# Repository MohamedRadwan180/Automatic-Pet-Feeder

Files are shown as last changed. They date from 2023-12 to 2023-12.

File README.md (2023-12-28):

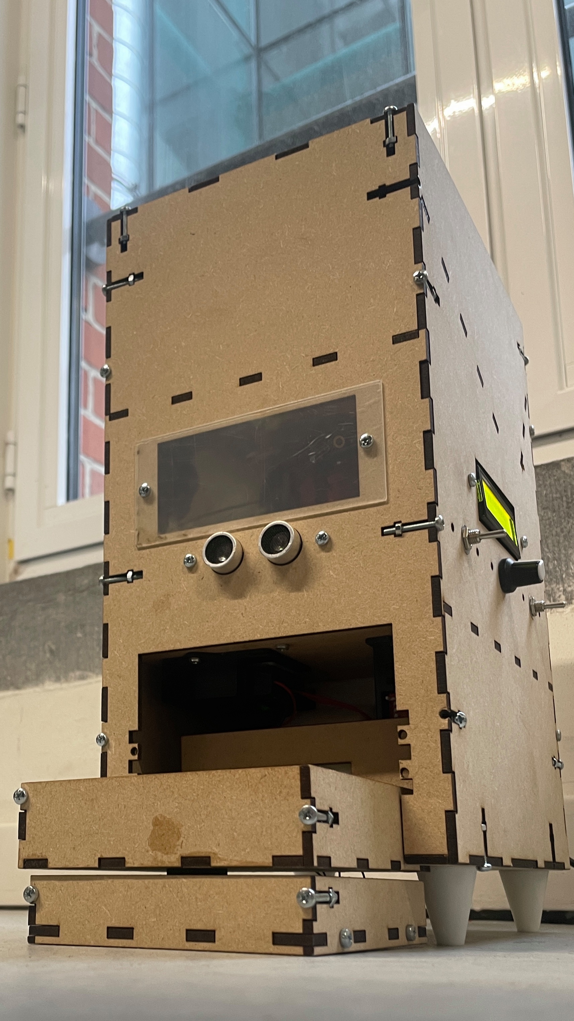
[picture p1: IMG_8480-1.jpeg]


This report describes the design and construction of the prototype of a “Cat Automatic Feeder and Entertainer” carried out in Design Methodology and Mechatronics 1 subjects at VUB as part of the Bruface master of mechantronics at VUB and ULB universities. The idea is simple: building a device that can take care of a cat during a long weekend, taking care of their nutrition and mental health. It will be able to feed the pet the appropriate amount of food at feeding times. In addition, whenever necessary, it will provide an entertaining game to clear the cat's mind. The origin of this idea stems from the lack of a complete product in the market and the need for cat owners to be unconcerned about their cats for a few days. 

The design will consider every possible constraint to achieve all the objectives, such as safety and correct feeding. The building has been developed by laser-cutting for simple and flat parts pieces and 3D printing for more complex ones. The whole design has been carefully designed to consider the space requirements of all components. The materials have been chosen to achieve ecological and functional requirements. 

The electronics and programming subsystems have been implemented in an Arduino Uno, using different modules to take every signal and control the actuators when necessary. Every sensor and motor has been deeply researched to understand the required power supply and code to define the inputs and outputs. 

Every subsystem has been tested before being implemented into the general system. In this way, unique errors can be detected and solved.

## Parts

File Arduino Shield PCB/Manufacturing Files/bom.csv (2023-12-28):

Designator | Footprint | Quantity | Value | LCSC Part #
A1 | Arduino_UNO_R3 | 1 | Arduino_UNO_R3
J1 | JST_EH_B4B-EH-A_1x04_P2.50mm_Vertical | 1 | Conn_01x04_Socket
J10, J7, J8 | TerminalBlock_bornier-2_P5.08mm | 3 | Conn_01x02_Pin
J11 | PinHeader_1x09_P2.54mm_Vertical | 1 | Conn_01x09_Pin
J12, J3, J4, J5 | PinHeader_1x03_P2.54mm_Vertical | 4 | Conn_01x03_Pin
J2, J6 | PinHeader_1x04_P2.54mm_Vertical | 2 | Conn_01x04_Pin
J9 | PinHeader_1x04_P2.54mm_Vertical | 1 | Conn_01x04_Socket

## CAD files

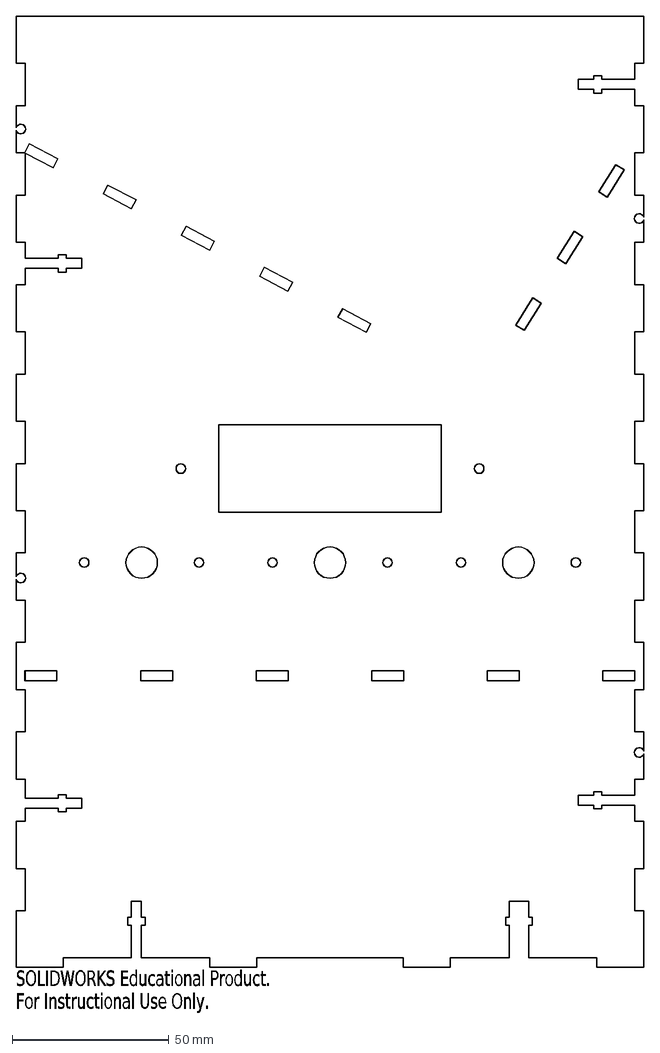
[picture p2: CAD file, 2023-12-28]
Mechanical Design CAD - Solidworks/CAT Feeder Box Franki/Pieza1-Brida base399.DXF
SOLIDWORKS Educational Product.
For Instructional Use Only.

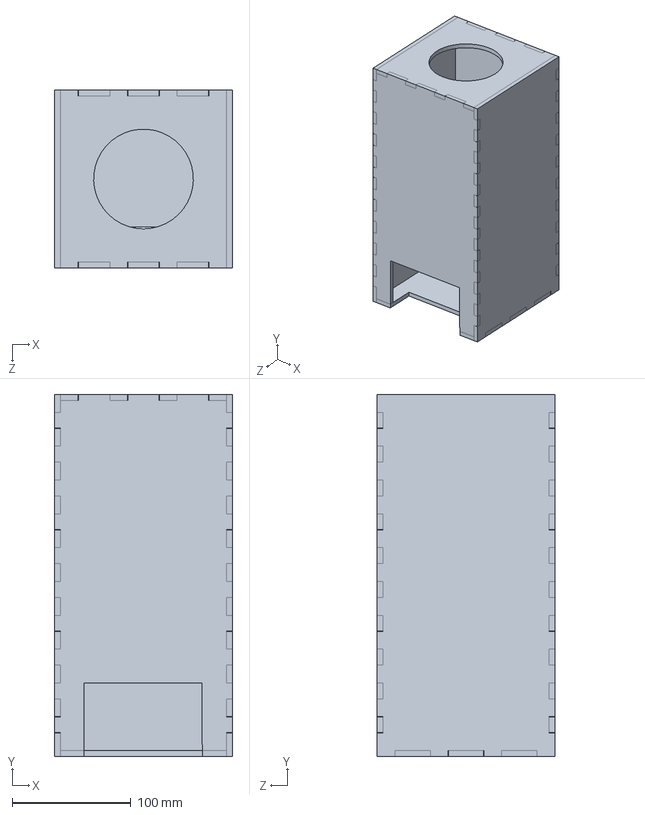
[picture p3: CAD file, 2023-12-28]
Mechanical Design CAD - Solidworks/cat feeder box-20231121T074059Z-001/cat feeder box/Pieza1.SLDPRT
150.0 x 305.0 x 150.0 mm

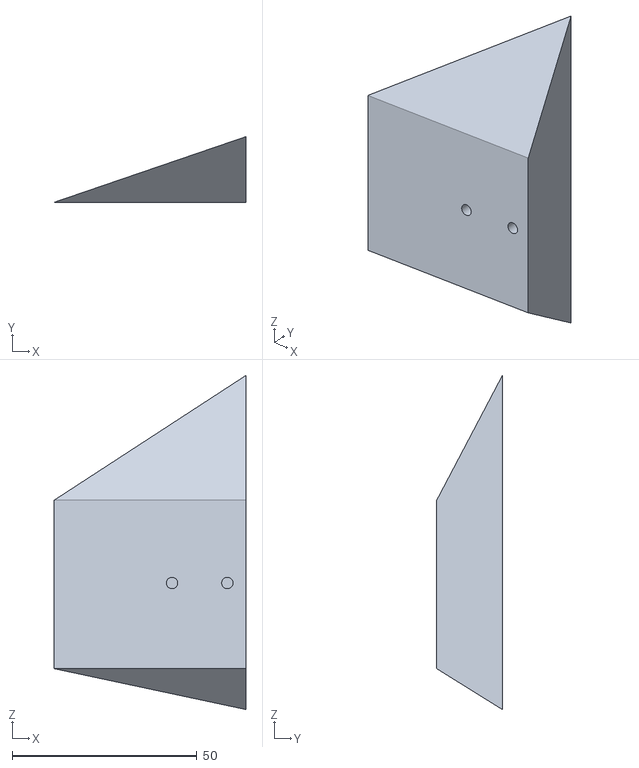
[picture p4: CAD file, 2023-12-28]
Mechanical Design CAD - Solidworks/Laser Pointing System/3d printing/Pieza1-Boss-Extrude4.STL
51.9 x 17.8 x 90.5

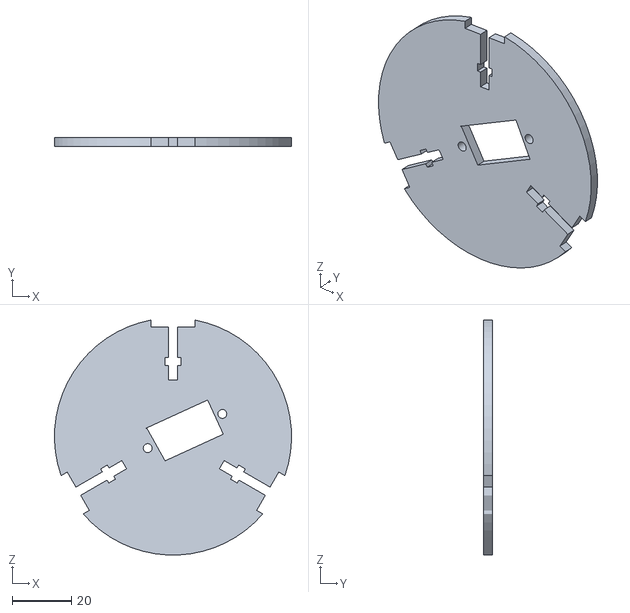
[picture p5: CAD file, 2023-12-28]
Mechanical Design CAD - Solidworks/Laser Pointing System/Motor Base Ring-Cut-Extrude5.STL
80.0 x 3.00 x 79.2

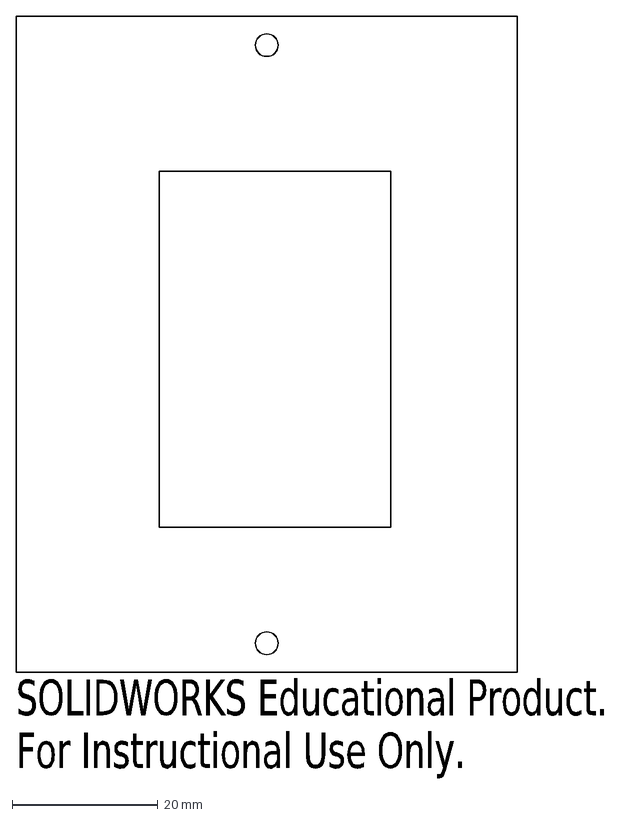
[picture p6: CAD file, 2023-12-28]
Mechanical Design CAD - Solidworks/Plate-Franki/laser cutter/case/Pieza1-Boss-Extrude8.DXF
SOLIDWORKS Educational Product.
For Instructional Use Only.

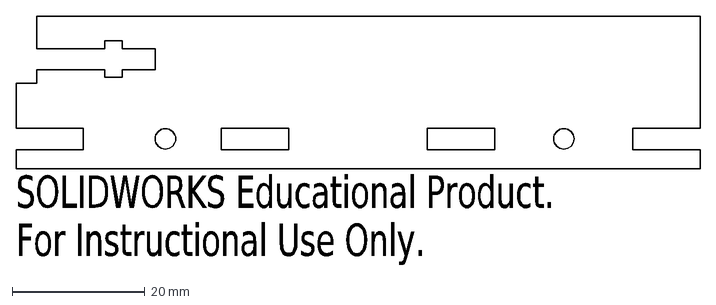
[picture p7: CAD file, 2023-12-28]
Mechanical Design CAD - Solidworks/Plate-Franki/laser cutter/plate/Pieza2-plate-Brida base7.DXF
SOLIDWORKS Educational Product.
For Instructional Use Only.

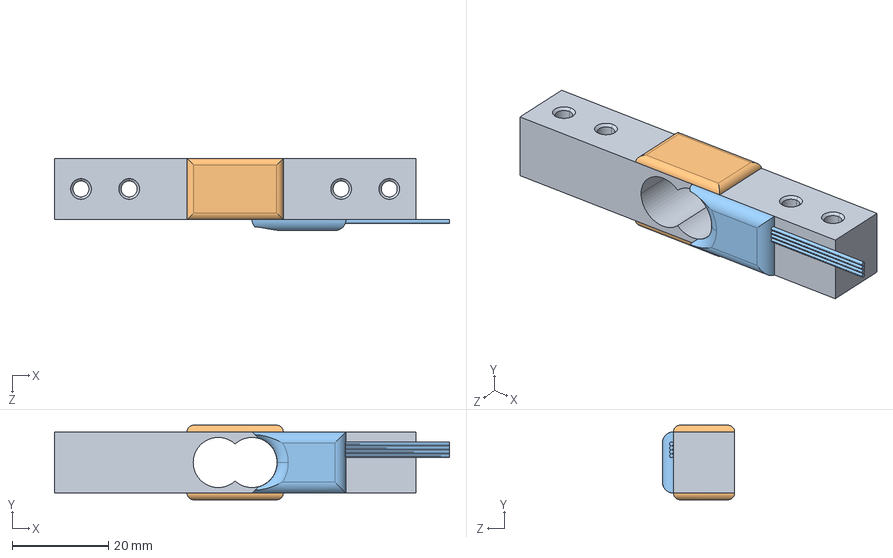
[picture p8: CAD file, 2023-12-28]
Mechanical Design CAD - Solidworks/Plate-Franki/Plate/weight sensor FHDA.STEP
82.0 x 15.5 x 15.0 mm

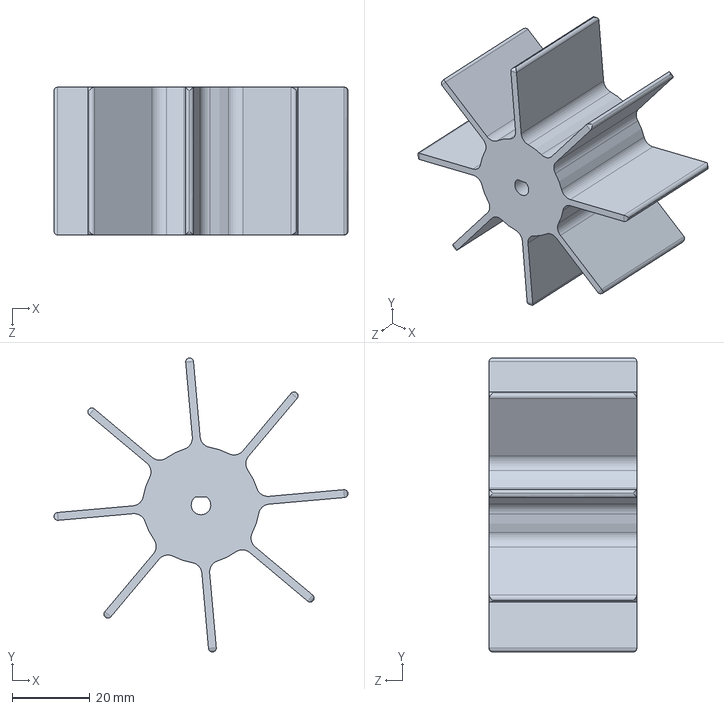
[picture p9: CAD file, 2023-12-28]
Mechanical Design CAD - Solidworks/wheel rotation/Food Dispenser-Boss-Extrude1.SLDPRT
75.6 x 75.6 x 38.0 mm

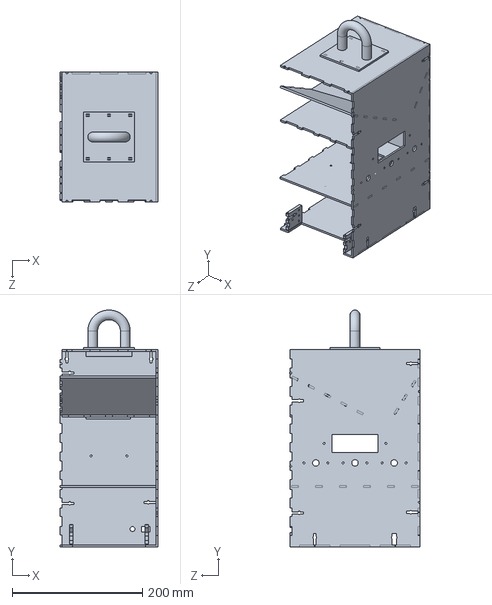
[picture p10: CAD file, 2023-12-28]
Mechanical Design CAD - Solidworks/CAT Feeder Box Franki/Pieza1.SLDPRT
150.0 x 363.5 x 200.0 mm

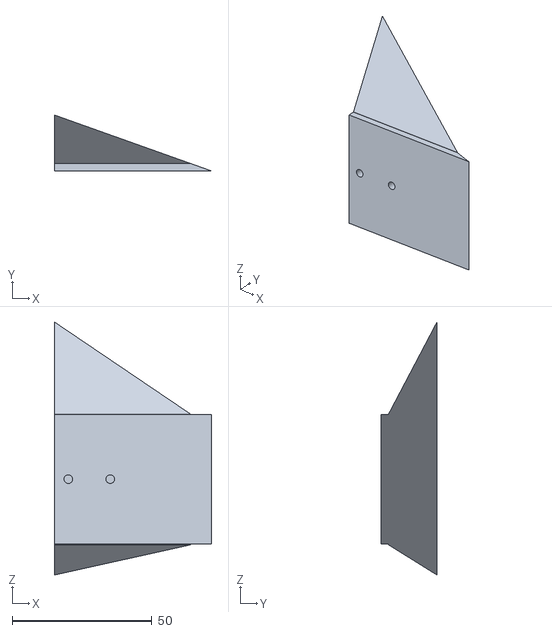
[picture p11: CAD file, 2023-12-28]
Mechanical Design CAD - Solidworks/Laser Pointing System/3d printing/Pieza1-Combine1.STL
56.2 x 20.0 x 90.5

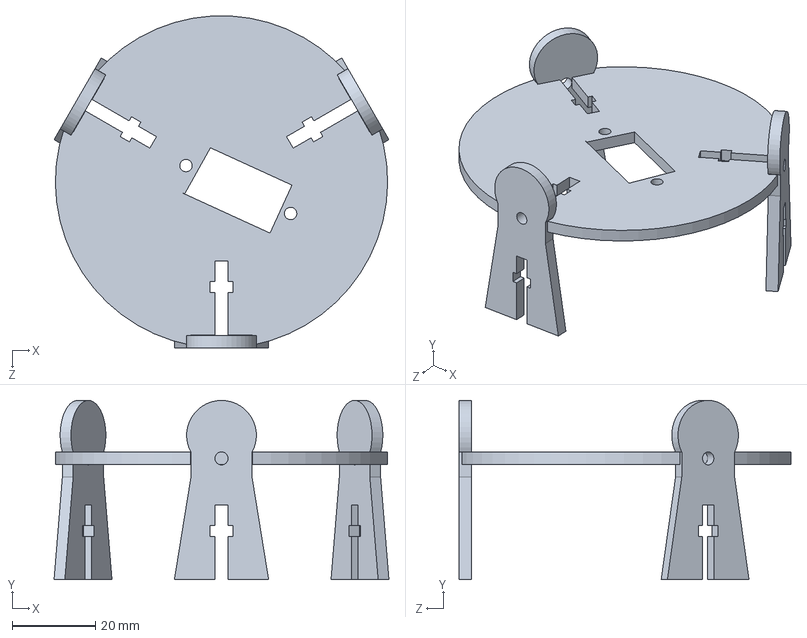
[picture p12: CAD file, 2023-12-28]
Mechanical Design CAD - Solidworks/Laser Pointing System/Motor Base Ring.SLDPRT
80.6 x 43.1 x 79.9 mm

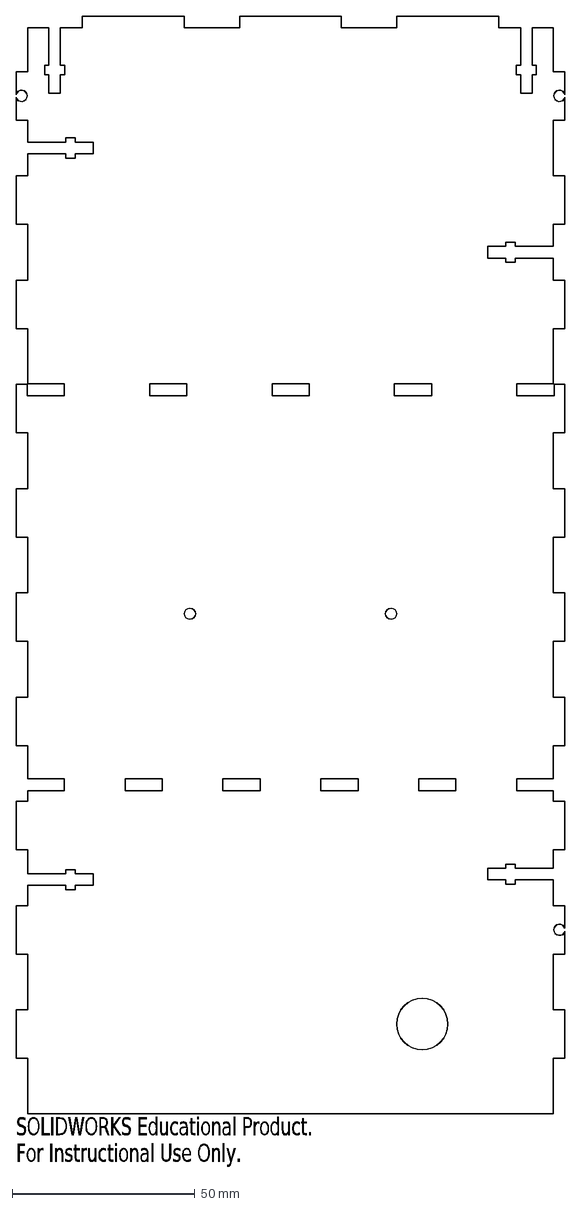
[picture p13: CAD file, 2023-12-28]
Mechanical Design CAD - Solidworks/Plate-Franki/laser cutter/case/Pieza1-Brida base4.DXF
SOLIDWORKS Educational Product.
For Instructional Use Only.

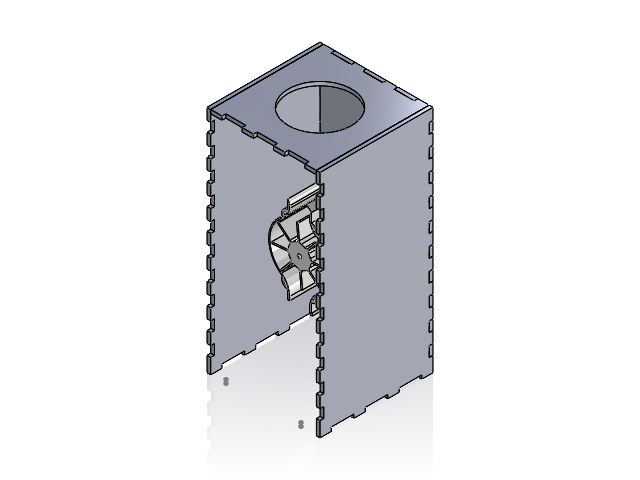
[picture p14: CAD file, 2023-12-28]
Mechanical Design CAD - Solidworks/Mechatronics_Full_Assembly.SLDASM
Pieza1
Food Dispenser
NEMA 17HS13-0404S1
Part1^Mechatronics_Full_Assembly

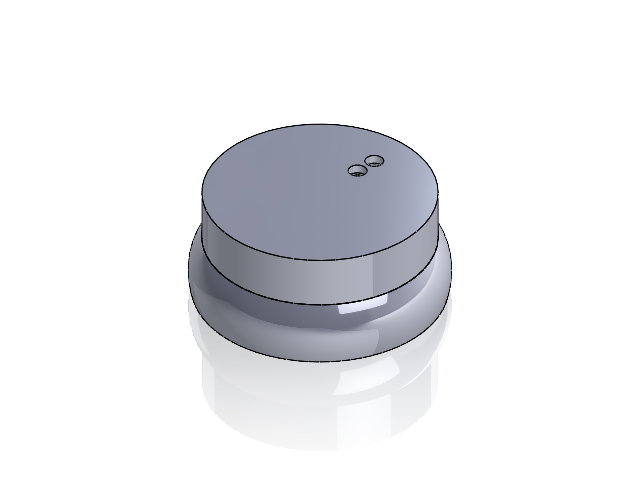
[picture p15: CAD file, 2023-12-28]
Mechanical Design CAD - Solidworks/Bowl_System.SLDASM
load cell sensor
Part1^Bowl_System
Part2^Bowl_System
Bowl
Part4^Bowl_System

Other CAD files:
Mechanical Design CAD - Solidworks/Laser Pointing System/Laser_Pointing.SLDASM
Mechanical Design CAD - Solidworks/Plate-Franki/Plate/Food-Plate.SLDASM
Mechanical Design CAD - Solidworks/Feeding_System.SLDASM
Mechanical Design CAD - Solidworks/cat feeder box-20231121T074059Z-001/cat feeder box/Dibujo Lcutter.DXF
Mechanical Design CAD - Solidworks/Bolt_Nut.SLDASM
Mechanical Design CAD - Solidworks/Bowl.SLDPRT
Mechanical Design CAD - Solidworks/CAT Feeder Box Franki/Pieza1-Brida base3-corrected.DXF
Mechanical Design CAD - Solidworks/CAT Feeder Box Franki/window.DXF
Mechanical Design CAD - Solidworks/CAT Feeder Box Franki/window.SLDPRT
Mechanical Design CAD - Solidworks/Dispenser_Holder.SLDPRT
Mechanical Design CAD - Solidworks/Food Dispenser.SLDPRT
Mechanical Design CAD - Solidworks/Leveling_Pins.SLDPRT
Mechanical Design CAD - Solidworks/Plate-Franki/Plate/111.DXF
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

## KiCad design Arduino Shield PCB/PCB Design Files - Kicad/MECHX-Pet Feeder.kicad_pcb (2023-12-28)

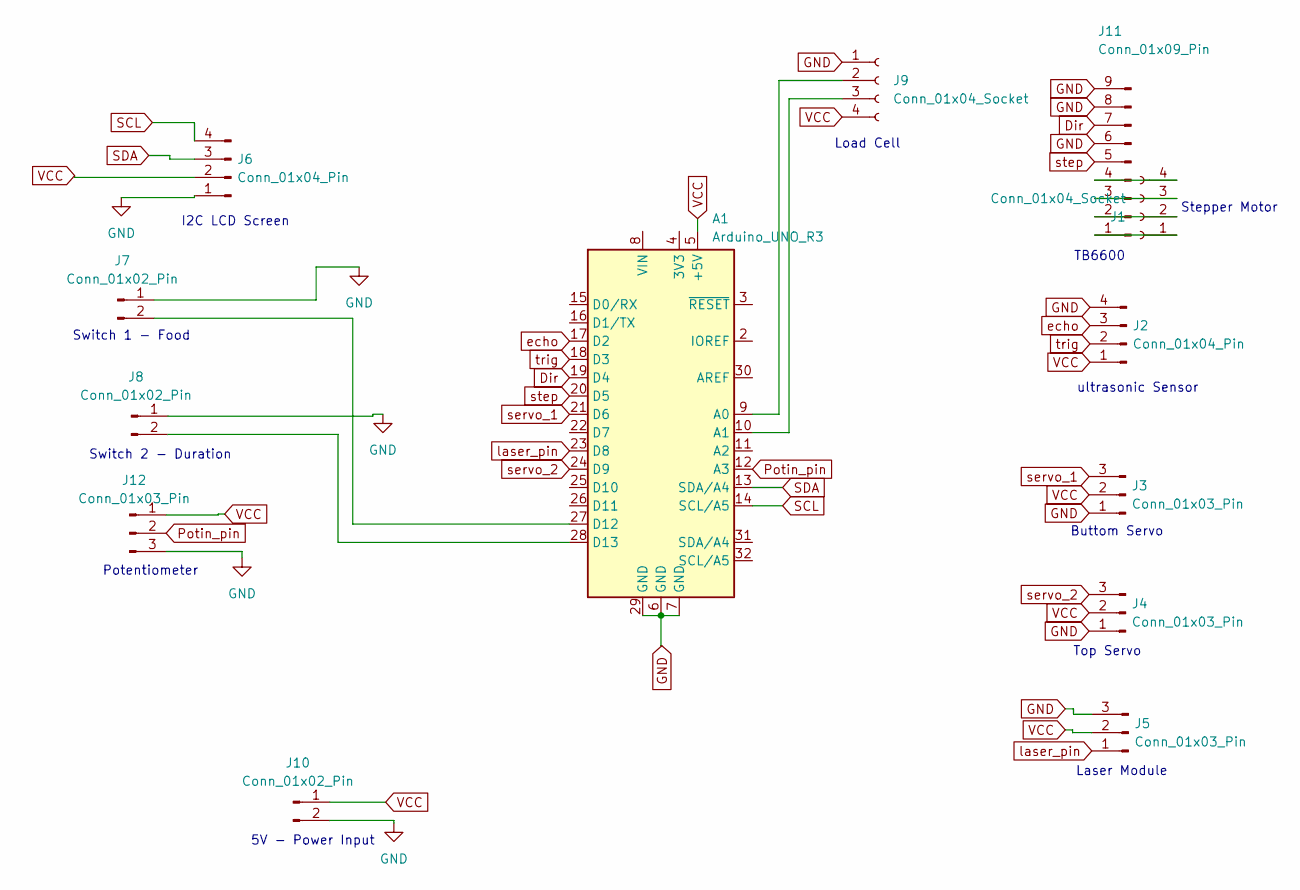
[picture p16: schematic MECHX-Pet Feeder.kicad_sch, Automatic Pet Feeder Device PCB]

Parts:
A1: Arduino_UNO_R3
J1: Conn_01x04_Socket; JST_EH_B4B-EH-A_1x04_P2.50mm_Vertical
J2, J6: Conn_01x04_Pin; PinHeader_1x04_P2.54mm_Vertical
J3, J4, J5, J12: Conn_01x03_Pin; PinHeader_1x03_P2.54mm_Vertical
J7, J8, J10: Conn_01x02_Pin; TerminalBlock_bornier-2_P5.08mm
J9: Conn_01x04_Socket; PinHeader_1x04_P2.54mm_Vertical
J11: Conn_01x09_Pin; PinHeader_1x09_P2.54mm_Vertical

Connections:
Dir: A1.19 (D4), J11.7
GND: A1.6 (GND), A1.7 (GND), A1.29 (GND), J2.4, J3.1, J4.1, J5.3, J6.1, J7.1, J8.1, J9.1, J10.2, J11.6, J11.8, J11.9, J12.3
unnamed: A1.9 (A0), J9.2
unnamed: A1.10 (A1), J9.3
unnamed: A1.27 (D12), J7.2
unnamed: A1.28 (D13), J8.2
unnamed: J1.1, J11.1
unnamed: J1.2, J11.2
unnamed: J1.3, J11.3
unnamed: J1.4, J11.4
Potin_pin: A1.12 (A3), J12.2
SCL: A1.14 (SCL/A5), J6.4
SDA: A1.13 (SDA/A4), J6.3
VCC: A1.5 (+5V), J2.1, J3.2, J4.2, J5.2, J6.2, J9.4, J10.1, J12.1
echo: A1.17 (D2), J2.3
laser_pin: A1.23 (D8), J5.1
servo_1: A1.21 (D6), J3.3
servo_2: A1.24 (D9), J4.3
step: A1.20 (D5), J11.5
trig: A1.18 (D3), J2.2

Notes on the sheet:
Switch 2 - Duration
5V - Power Input
Laser Module
Buttom Servo
Top Servo
Load Cell
I2C LCD Screen
ultrasonic Sensor
TB6600
Potentiometer
Stepper Motor
Switch 1 - Food

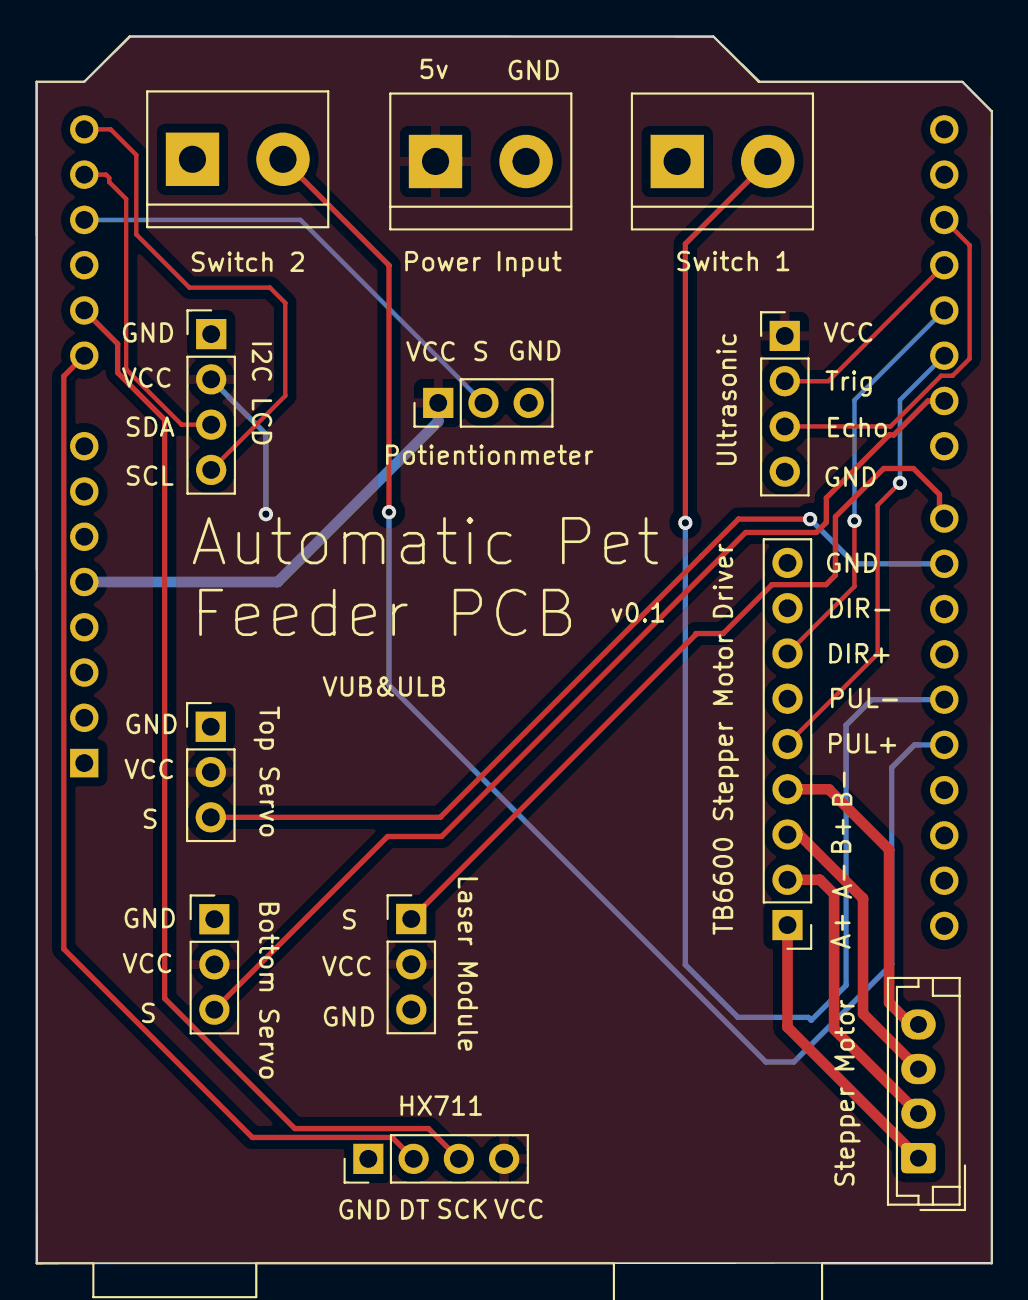
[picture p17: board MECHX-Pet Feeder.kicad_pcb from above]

Board: 2 copper layers, 53.6 x 68.9 mm, 13 parts (0 on the bottom side), 20 nets.

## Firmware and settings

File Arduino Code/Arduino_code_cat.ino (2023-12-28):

#include "HX711.h"
#include <Wire.h>
#include <LiquidCrystal_I2C.h>
#include <Servo.h>

#define dirPin 4
#define stepPin 5
#define FstepsPerRevolution 99
#define BstepsPerRevolution 50
// HX711 circuit wiring
const int Load_cell_DOUT_pin = A0;
const int LOad_cell_SCK_pin = A1;
bool first_time = true;
float c;
HX711 scale;
float weight_2;

//interface
LiquidCrystal_I2C lcd(0x27, 16, 2);  // Déclare l'écran LCD I2C avec son adresse et dimensions (16 colonnes et 2 lignes)
int switch_1_food_amount = 12;
int switch_2_duration = 13;
int potint = A3;
int potint_val = 0;
int portion_size = 10;
int food_duration = 10000; 
int food_status;
int timing_status;

long current_time;
long start_program;

//Entertainment
Servo servoX;
Servo servoY;
/////// Pin laser 
const int laserPin = 8; // Laser control pin
int posX = 90; // Initial position on X axis
int posY = 90; // Initial position on Y axis

// Total number of points to draw
int totalPoints = 10;
int laserDelay = 200; // Laser flash delay (in milliseconds)
int moveDelay = 500; // Delay between moves (in milliseconds)
int enter_start_time;
int enter_current_time;

////// Code for the ultrasonic sensor
float distance;
int currentState;
bool previousState = false; // the cat is not detected. Initial status
const int echoPin_ultrasonic = 2;
const int trigPin_ultrasonic = 3;
int entertainment_limit = 400;
//////

void initiate_settings()
{
  food_status = digitalRead(switch_1_food_amount);
  Serial.println(food_status);

  if(food_status == 1)
  {
    lcd.setCursor(0, 0);
    lcd.print("Portion Size?");
       lcd.setCursor(15, 1);
      lcd.print("g");
  while(food_status == 1)
  {
    
    potint_val = analogRead(potint);
    portion_size = map(potint_val, 0, 1023, 0, 200);
    food_status = digitalRead(switch_1_food_amount);
      lcd.setCursor(0, 1);
      lcd.print(portion_size);
   
      delay(100);
  }
  }
  else
  {
    lcd.clear();
  }

    timing_status = digitalRead(switch_2_duration);
  Serial.println(timing_status);

  if(timing_status == 1)
  {
    lcd.setCursor(0, 0);
    lcd.print("Feeding Duration?");
       lcd.setCursor(13, 1);
      lcd.print("sec");
  while(timing_status == 1)
  {
    
    potint_val = analogRead(potint);
    food_duration = map(potint_val, 0, 1023, 0, 30000);
    timing_status = digitalRead(switch_2_duration);
      lcd.setCursor(0, 1);
      lcd.print(food_duration/1000);
      delay(100);
  }
  }
  else
  {
    lcd.clear();
  }
}

void Dispense(){

    // Set the spinning direction counterclockwise:
  digitalWrite(dirPin, LOW);

  // Spin the stepper motor 1 revolution slowly:
  for (int i=0; i < BstepsPerRevolution; i++) {
    // These four lines result in 1 step:
    digitalWrite(stepPin, HIGH);
    delayMicroseconds(800);
    digitalWrite(stepPin, LOW);
    delayMicroseconds(800);
  }

  delay(100);
     // Set the spinning direction clockwise:
  digitalWrite(dirPin, HIGH);

  // Spin the stepper motor 1 revolution slowly:
  for (int i=0; i < FstepsPerRevolution; i++) {
    // These four lines result in 1 step:
    digitalWrite(stepPin, HIGH);
    delayMicroseconds(600);
    digitalWrite(stepPin, LOW);
    delayMicroseconds(600);
  }

  delay(1000);
}

void activ_laser() {

  for (int i = 0; i < totalPoints; ++i) {
    // Generate random coordinates over a 0.25 m² area (0.5 m x 0.5 m)
    int targetX = random(50, 200); // Range 50 to 200 (0.05 to 0.20 m)
    int targetY = random(50, 200); // Range 50 to 200 (0.05 to 0.20 m)

    // Convertir les coordonnées en positions pour les servomoteurs
    int servoPosX = map(targetX, 50, 200, 50, 120); // Convert range to degrees for X (servo)
    int servoPosY = map(targetY, 100, 200, 140, 150); // Convert range to degrees for Y (servo)

    // Move servos to target coordinates
    servoX.write(servoPosX);
    servoY.write(servoPosY);

    // Activate laser (flashing)
    digitalWrite(laserPin, HIGH);
    delay(laserDelay); // Flash delay

    // Deactivate laser
    digitalWrite(laserPin, LOW);

    // Wait before moving on to the next item
    delay(moveDelay);
  }

}

float fun_distance() {
  // Clear the Trigger pin
  digitalWrite(trigPin_ultrasonic, LOW);
  delayMicroseconds(2);
  // Set the Trigger pin high for 10 microseconds
  digitalWrite(trigPin_ultrasonic, HIGH);
  delayMicroseconds(10);
  digitalWrite(trigPin_ultrasonic, LOW);

  // Read the pulse time on Echo pin
  float duration = pulseIn(echoPin_ultrasonic, HIGH);

  // Calculate the distance
  distance = duration * 0.34 / 2; // Speed of sound: 343 m/s

  // Display the distance on the Serial Monitor
  // Serial.print("Distance: ");
  // Serial.println(distance);
  return distance; //in milimeters
}

void setup() {
    //////// Setup ultrasonic senosr pins 
  pinMode(echoPin_ultrasonic, INPUT);  // Pin 2    Set the Echo pin as an input
  pinMode(trigPin_ultrasonic, OUTPUT); // Pin 3    Set the Trigger pin as an output
  Serial.begin(9600);       // Initialize serial communication
  // Also Vcc + GND
  //////// 
  // put your setup code here, to run once:
  Serial.begin(9600);
  scale.begin(Load_cell_DOUT_pin, LOad_cell_SCK_pin);

  // Declare pins as output:
  pinMode(stepPin, OUTPUT);
  pinMode(dirPin, OUTPUT);

    //initiating switches
  pinMode(switch_1_food_amount, INPUT_PULLUP);
  pinMode(switch_2_duration, INPUT_PULLUP);
  //initiating LCD
  lcd.init();                      // Initialize the LCD screen
  lcd.backlight();                 // Activate the screen backlight
  start_program = millis();


    /////// Servo-motor code
  servoX.attach(6);  // Pin 6 + Vcc + GND    Attach the first servo (modifiable according to your wiring)
  servoY.attach(9); // Pin 9 + Vcc + GND    Attach the second servo (modifiable according to your wiring)
  ///////

  /////// Laser 
  pinMode(laserPin, OUTPUT); // Pin 8 + Vcc + GND
  ///////
}




void loop() { // Main loop, where all the functions are called. Here starts the WAIT block of the FLow Diagram
  lcd.clear();    
  initiate_settings();
  current_time = millis();
   Serial.println(scale.is_ready());
    if (scale.is_ready()) {         // Take weight measurements from the sensor
    weight_2 = scale.get_units(10); // Average of 10 readings
    if (first_time == true){
      c = -weight_2*0.0026;         // The first time that the system is working, with the tray empty, 
                                    // measurement subsystem is calibrated.
      first_time = false;
    }
    Serial.print("Weight: ");
    Serial.print(weight_2*0.0026 + c); // Two decimal places
    Serial.println(" g");
    lcd.setCursor(0, 0);
    lcd.print("Weight: ");
    lcd.setCursor(9, 0);
    lcd.print((weight_2*0.0026 + c));
    lcd.setCursor(0, 1);
    lcd.print("Feed in: ");
    lcd.setCursor(14, 1);
    lcd.print("s");
    lcd.setCursor(9, 1);
    lcd.print((food_duration/1000) - ((current_time-start_program)/1000));
    
    if(current_time-start_program>=food_duration) // check if it is time to feed
    {
    if(weight_2*0.0026 + c < portion_size)        // check if the tray has enought food
    {
    while(weight_2*0.0026 + c < portion_size)      // dispense food until the limit has been reached
    {
      lcd.clear();
      lcd.setCursor(0, 0);
      lcd.print("Time to feed......");
      lcd.setCursor(0, 1);
      lcd.print("Food: ");
      lcd.setCursor(12, 1);
      lcd.print("g");
      Dispense();                                 // function to dispense food
      //tart_program = current_time;
      weight_2 = scale.get_units(10); 
      delay(1000);
      start_program = current_time;               // set the current time as the last time that food has been given
      lcd.setCursor(7, 1);
      lcd.print(weight_2*0.0026 + c);
    }
    }else{
      lcd.clear();
      lcd.setCursor(0, 0);
      lcd.print("Tray is full");                  // else, say that the tray is full
      delay(3000);
      lcd.clear();
    }
        start_program = current_time;

    }
  } else {
    Serial.println("HX not working!!");
  }

  if(fun_distance() <= entertainment_limit)     // check if the cat is nearby
  {
    activ_laser();                              // entertain the cat and give food reward
    Dispense();
  }

  delay(1000);                                  // 1s delay to avoid probelms with the weight sensor measurements
}

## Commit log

2023-12-28 CAD Added
    [111.DXF, 111.SLDPRT, 222.DXF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]
2023-12-28 Arduino Code
